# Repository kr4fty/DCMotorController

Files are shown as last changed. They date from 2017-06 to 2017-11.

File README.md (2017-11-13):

# DCMotorController

Control de lazo cerrado para motores DC utilizando un ATMEGA328p (corazón del
  Arduino UNO) y un puente H tipo L293.

<!-- TOC depthFrom:1 depthTo:6 withLinks:1 updateOnSave:1 orderedList:0 -->

- [DCMotorController](#dcmotorcontroller)
	- [Descripción](#descripcin)
	- [Funcionamiento](#funcionamiento)
		- [Parámetros PID](#parmetros-pid)
	- [Características:](#caractersticas)
	- [Firmware](#firmware)
		- [Dependencias](#dependencias)
	- [Hardware](#hardware)
		- [Esquematico](#esquematico)
	- [Video](#video)
	- [Motores de corriente continua](#motores-de-corriente-continua)
		- [Ventajas de los Motores DC frente a los PaP](#ventajas-de-los-motores-dc-frente-a-los-pap)
		- [Desventajas de los Motores DC frente a los PaP](#desventajas-de-los-motores-dc-frente-a-los-pap)
	- [Proyectos Similares](#proyectos-similares)
	- [Licencia](#licencia)
	- [Autor](#autor)

<!-- /TOC -->

<p align="center">
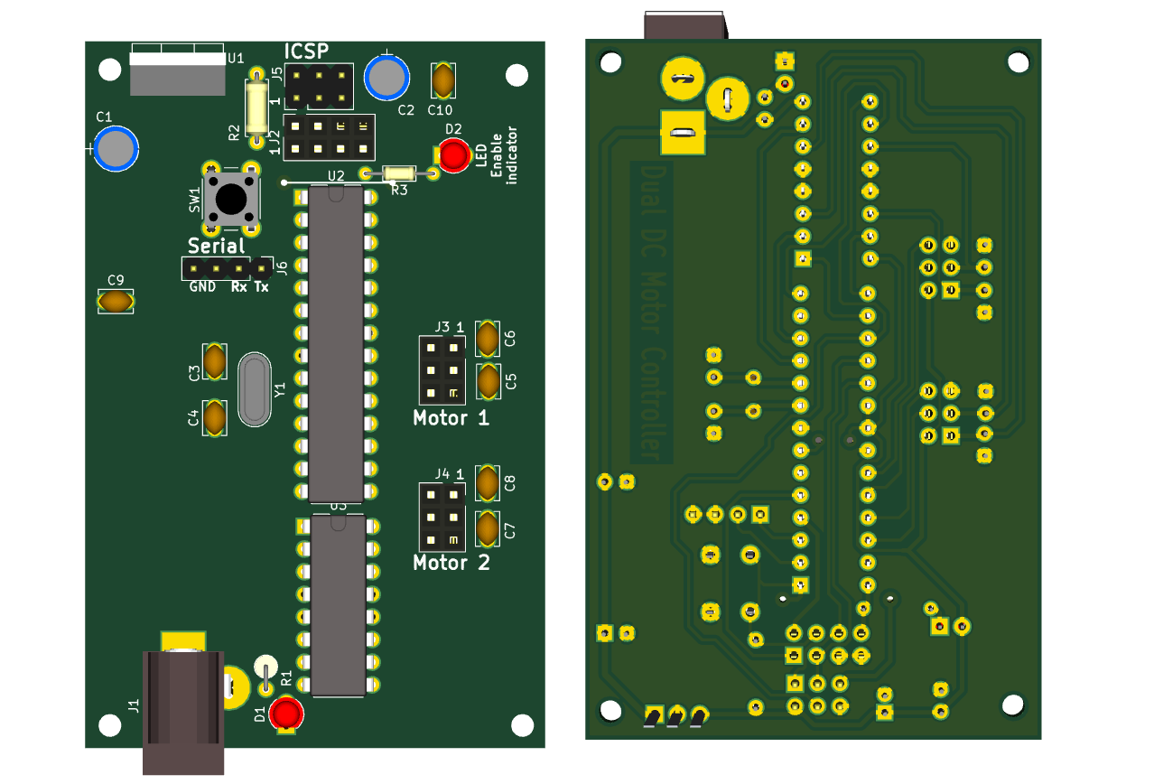
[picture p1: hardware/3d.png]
  
</p>

## Descripción
Este es una pequeña implementación de la librería [ArduinoPID](https://github.com/br3ttb/Arduino-PID-Library), para el control
de motores de corriente continua, DC, que cuenten con un encoder acoplado a su
eje.

Cuenta con soporte para **uno** o **dos** motores, dependiendo de como este
configurado dentro de _**motor.h**_.

La idea principal del proyecto es la de utilizar MOTORES DC/Servos en proyectos
de construcción de CNC en lugar de los tradicionales Motores Paso a Paso (PaP).

El sistema es compatible a nivel de pins de control, con los driver para motores
PaP, **STEP** y **DIR**, como por ejemplo el [Pololu A4988](https://www.pololu.com/product/1182).

## Funcionamiento
Un Arduino cargado con **GRBL**, por ejemplo, envía un pulso a través del pin **STEP**. Cada pulso que recibe el driver le dice al motor que tiene que avanzar un micropaso.

Luego por medio del pin **DIR** obtenemos la dirección de avance, si queremos ir en el sentido de las agujas del reloj, o al contrario.

De esta forma, cada vez que el driver recibe un pulso en el pin **STEP**, el circuito comprueba el estado del pin **DIR**, y alimenta las bobinas del motor en el orden adecuado.

### Parámetros PID
El proceso de sintonizado del PID se hizo de forma experimental, prueba/error, tratando de tener tanto el **overshoot** como el **tiempo de establecimiento** los mas chicos posibles.
Se llego a la conclusión que para el par de motores utilizados, los parámetros que mejor se ajustaban fueron los siguientes:

  * Setpoint > 50: </br>
      Kp = 10 // Agresive Kp</br>
      Ki = 1 // Agresive Ki</br>
      Kd = 0.01 // Agresive Kd</br>

  * Setpoint =< 50:</br>
      Kp = 5  // Conservative Kp</br>
      Ki = 0.1  // Conservative Ki</br>
      Kd = 0.001  // Conservative Kd</br>

Dependiendo del tipo de Motor/Servo utilizados, estos parámetros deberán ser cambiados. Esto ultimo se realizara modificando los prarametros AGGKp,AGGKi, AGGKd, CONSKp, CONSKi y CONSKd, dentro de **motor.h**

## Características:
  * El conjunto Driver-Servo/Motor remplaza al conjunto Driver-Motor/PaP
  * El corazón del sistema es un chip **ATMEGA328p**
  * Se puede controlar uno o dos motores simultáneamente
  * El Driver tiene cuatro señales de control: **DIR**, **STEP**, **ENABLE** y **RESET**
  * Cada motor puede ser controlado de forma independiente por medio de **DIR** y
    **STEP**
  * El sistema de control esta basado en un sistema PID
  * El PWM trabaja a una frecuencia de 31.25KHz, imperceptible al oído humano
  * Cuenta con un salida por puerto serie para depuración
  * Tanto las señales de entrada de los STEPs como las de los encoders, utilizan
    interrupciones del tipo **PIN CHANGE** (PCI)
  * El diseño del **PCB** fue realizado en [KiCAD](https://github.com/KiCad/)
  * La etapa de potencia de los motores fue realizada con un **puente H** del tipo L293D

## Firmware
### Dependencias
El proyecto depende de cuatro librerías:
  * [ArduinoPID](https://github.com/br3ttb/Arduino-PID-Library): Librería principal con la que se realiza el control de lazo
    cerrado
  * [EnableInterrupt](https://github.com/GreyGnome/EnableInterrupt): Encargada de vincular las interrupciones del tipo Pin-change con la respectiva ISR.
  * [EncoderPCI](https://github.com/kr4fty/EncoderPCI): Librería encargada de manejar los Encoders
  * [DCMotorServoPCI](https://github.com/kr4fty/DCMotorServoPCI): Es la librería en si, que realiza la gestión y el control del
    motor dc

## Hardware
Pins utilizados:

<table>
	<tr><th></th><th> Motor 1 </th></tr>
	<tr><th> <b>Arduino Pin</b> </th><th> <b>Descripción</b> </th></tr>
	<tr><td>10 </td><td> pwmX, chip enable 1 del L293D </td></tr>
	<tr><td>6  </td><td> in1X, salida hacia el pin 2, IN1, del L293D </td></tr>
	<tr><td>5  </td><td> in2X, salida hacia el pin 7, IN2, del L293D </td></tr>
	<tr><td>A2 </td><td> inAX, entrada A desde el encoder </td></tr>
	<tr><td>A3 </td><td> inBX, entrada B desde el encoder </td></tr>
	<tr><td>2  </td><td> stepX, entrada STEP proveniente del otro Arduino cargado con GRBL </td></tr>
	<tr><td>12 </td><td> dirX, entrada DIR proveniente del otro Arduino cargado con GRBL </td></tr>
</table>

<table>
	<tr><th></th><th> Motor 2 </th></tr>
	<tr><th> <b>Arduino Pin</b> </th><th> <b>Descripción</b> </th></tr>
	<tr><td> 11 </td><td> pwmY, chip enable 2 del L293D </td></tr>
	<tr><td> 8 </td><td> in1Y, salida hacia el pin 10, IN3, del L293D </td></tr>
	<tr><td> 9 </td><td> in2Y, salida hacia el pin 15, IN4, del L293D </td></tr>
	<tr><td> A0 </td><td> inAY, entrada A desde el encoder </td></tr>
	<tr><td> A1 </td><td> inBY, entrada B desde el encoder </td></tr>
	<tr><td> 3 </td><td> stepY, entrada STEP </td></tr>
	<tr><td> 13 </td><td> dirY, entrada DIR </td></tr>
</table>

<table>
	<tr><th></th><th> Global </th></tr>
	<tr><th> <b>Arduino Pin</b> </th><th> <b>Descripción</b> </th></tr>
	<tr><td> A5 </td><td> entrada ENABLE </td></tr>
	<tr><td> Rst </td><td> Reset del driver </td></tr>
</table>

### Esquematico

<p align="center">
  <br><br>
  <b>Circuito</b><br>
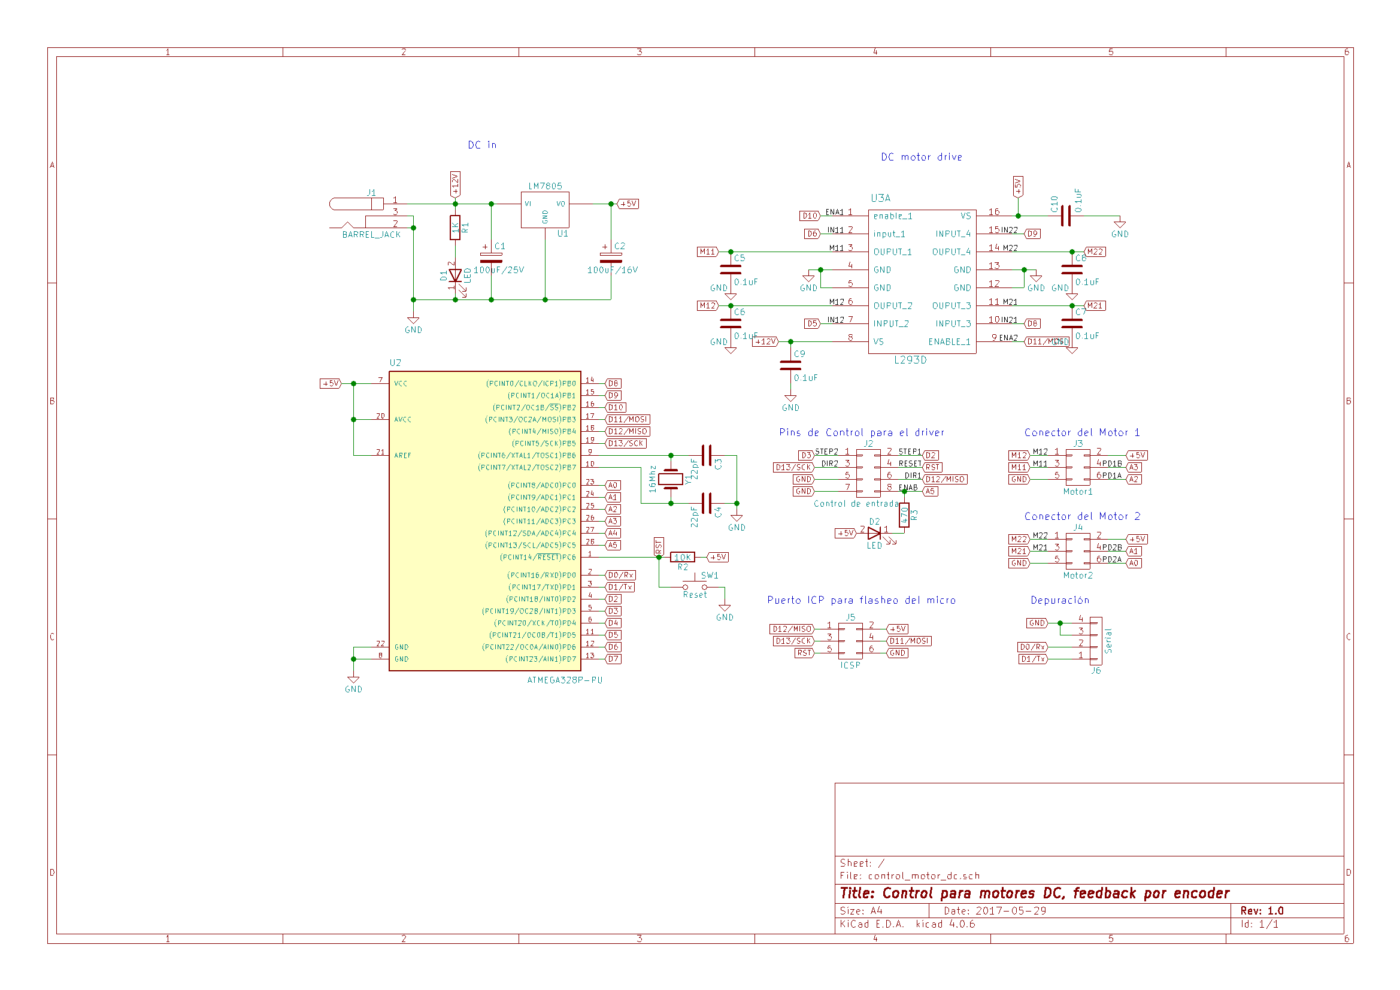
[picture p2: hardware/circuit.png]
  
  <br>
</p>

## Video
<p align="center">
  <b>YouTube</b><br>
  <a href="https://www.youtube.com/watch?v=HcTcVE0kusM">
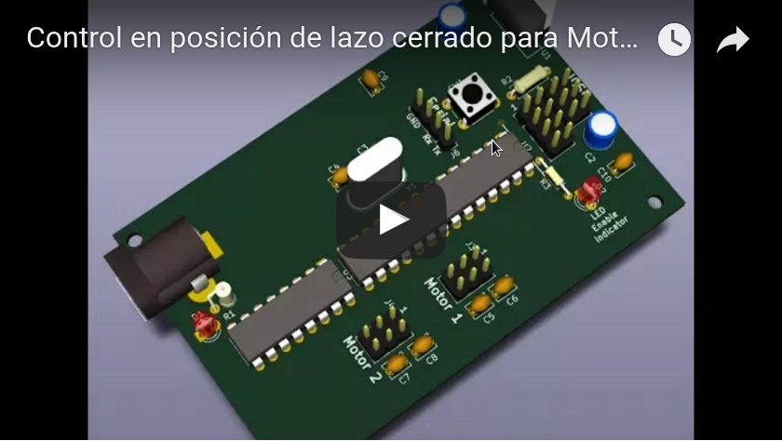
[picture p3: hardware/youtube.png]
  
  </a>
</p>

## Motores de corriente continua

### Ventajas de los Motores DC frente a los PaP
  * Poseen gran velocidad de giro
  * Alta aceleración/Par inicial
  * Son silenciosos
  * Movimiento suave y sin saltos
  * Control medianamente sencilla
  * Electrónica mas sencilla
  * Utiliza realimentación para el control del sistema
  * Debido a este ultimo, tiene alta precisión en posición (depende fuertemente
    del encoder acoplado)

### Desventajas de los Motores DC frente a los PaP
  * La potencia de funcionamiento pico sólo se desarrolla a altas velocidades
  * Debido a sus altas velocidades estos pueden calentarse mas rápidamente
    (podría necesitar un sistemas de ventilación)
  * Inercia mas elevada (depende de la  velocidad y la carga acoplada al eje)

## Proyectos Similares
  * [ServoStrap](https://github.com/danithebest91/ServoStrap) por _danithebest91_
  * [SuryaProCell-CNC](https://github.com/suryaprocell/SuryaProCell-CNC) por _suryaprocell_
  * [DC-Servo-Controller](https://github.com/makerbot/DC-Servo-Controller) por _makerbot_
  * [dcservo](https://github.com/misan/dcservo) por _misan_

## Licencia

GPLv2

## Autor

Tapia Favio

## Feedback

Por favor agradecería que me envies cualquier duda y/o comentario para mejorar el proyecto, gracias.

Mail: technicc (at) gmail.com

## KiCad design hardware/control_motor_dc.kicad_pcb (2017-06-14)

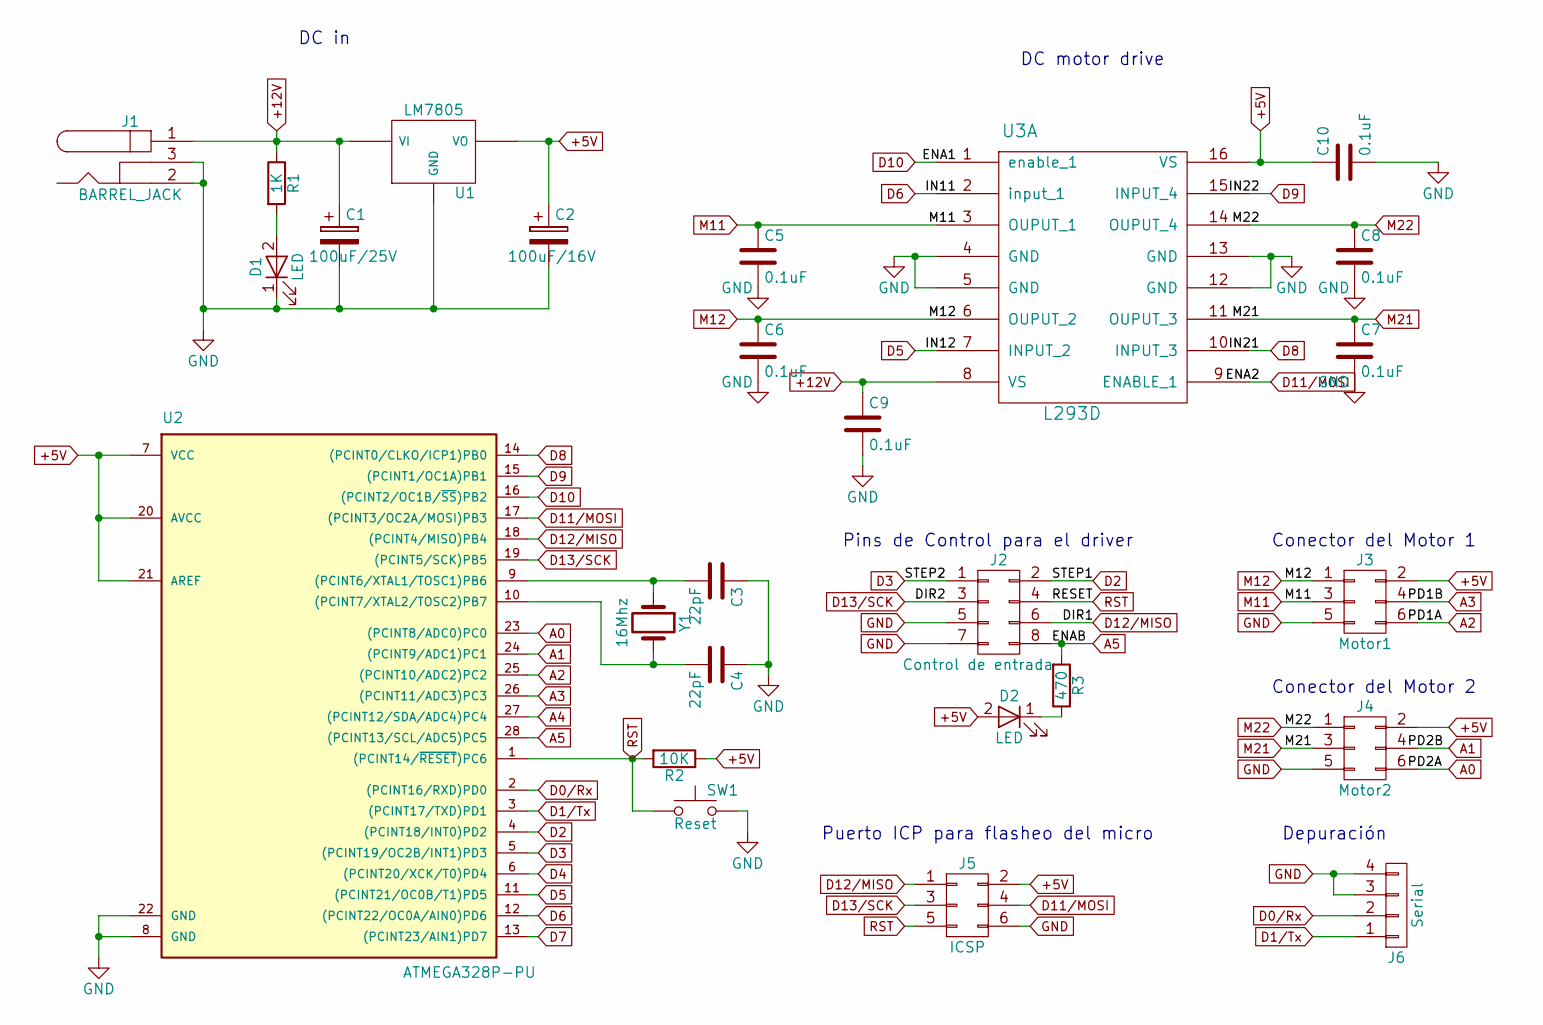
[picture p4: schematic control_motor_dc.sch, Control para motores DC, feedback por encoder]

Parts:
C1: 100uF/25V; CP_Radial_D5.0mm_P2.50mm
C2: 100uF/16V; CP_Radial_D5.0mm_P2.00mm
C3, C4: 22pF; C_Disc_D3.8mm_W2.6mm_P2.50mm
C5, C6, C7, C8, C9, C10: 0.1uF; C_Disc_D3.8mm_W2.6mm_P2.50mm
D1, D2: LED; LED_D3.0mm
J1: BARREL_JACK; JACK_ALIM
J2: Control de entrada; Socket_Strip_Straight_2x04_Pitch2.54mm
J3: Motor1; Socket_Strip_Straight_2x03_Pitch2.54mm
J4: Motor2; Socket_Strip_Straight_2x03_Pitch2.54mm
J5: ICSP; Pin_Header_Straight_2x03_Pitch2.54mm
J6: Serial; Pin_Header_Straight_1x04_Pitch2.54mm
R1: 1K; R_Axial_DIN0207_L6.3mm_D2.5mm_P2.54mm_Vertical
R2: 10K; R_Axial_DIN0207_L6.3mm_D2.5mm_P7.62mm_Horizontal
R3: 470; R_Axial_DIN0204_L3.6mm_D1.6mm_P7.62mm_Horizontal
SW1: Reset; SW_PUSH_6mm
U1: LM7805; TO-220_Vertical-fav
U2: ATMEGA328P-PU; DIP-28_W7.62mm
U3: L293D; DIP-16_W7.62mm
Y1: 16Mhz; Crystal_HC52-6mm_Vertical

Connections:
+5V: C2.1, C10.1, D2.2 (A), J3.2, J4.2, J5.2, R2.1, U1.VO, U2.7 (VCC), U2.20 (AVCC), U2.21 (AREF), U3.16 (VS)
+12V: C1.1, C9.1, J1.1, R1.1, U1.VI, U3.8 (VS)
A0: J4.6, U2.23 ((PCINT8/ADC0)PC0)
A1: J4.4, U2.24 ((PCINT9/ADC1)PC1)
A2: J3.6, U2.25 ((PCINT10/ADC2)PC2)
A3: J3.4, U2.26 ((PCINT11/ADC3)PC3)
A4: U2.27 ((PCINT12/SDA/ADC4)PC4)
A5: J2.8, R3.2, U2.28 ((PCINT13/SCL/ADC5)PC5)
D0/Rx: J6.2, U2.2 ((PCINT16/RXD)PD0)
D1/Tx: J6.1, U2.3 ((PCINT17/TXD)PD1)
D2: J2.2, U2.4 ((PCINT18/INT0)PD2)
D3: J2.1, U2.5 ((PCINT19/OC2B/INT1)PD3)
D4: U2.6 ((PCINT20/XCK/T0)PD4)
D5: U2.11 ((PCINT21/OC0B/T1)PD5), U3.7 (INPUT_2)
D6: U2.12 ((PCINT22/OC0A/AIN0)PD6), U3.2 (input_1)
D7: U2.13 ((PCINT23/AIN1)PD7)
D8: U2.14 ((PCINT0/CLKO/ICP1)PB0), U3.10 (INPUT_3)
D9: U2.15 ((PCINT1/OC1A)PB1), U3.15 (INPUT_4)
D10: U2.16 ((PCINT2/OC1B/~SS~)PB2), U3.1 (enable_1)
D11/MOSI: J5.4, U2.17 ((PCINT3/OC2A/MOSI)PB3), U3.9 (ENABLE_1)
D12/MISO: J2.6, J5.1, U2.18 ((PCINT4/MISO)PB4)
D13/SCK: J2.3, J5.3, U2.19 ((PCINT5/SCK)PB5)
GND: C1.2, C2.2, C3.1, C4.1, C5.2, C6.2, C7.2, C8.2, C9.2, C10.2, D1.1 (K), J1.2, J1.3, J2.5, J2.7, J3.5, J4.5, J5.6, J6.3, J6.4, SW1.2, U1.GND, U2.8 (GND), U2.22 (GND), U3.4 (GND), U3.5 (GND), U3.12 (GND), U3.13 (GND)
M11: C5.1, J3.3, U3.3 (OUPUT_1)
M12: C6.1, J3.1, U3.6 (OUPUT_2)
M21: C7.1, J4.3, U3.11 (OUPUT_3)
M22: C8.1, J4.1, U3.14 (OUPUT_4)
unnamed: C3.2, U2.9 ((PCINT6/XTAL1/TOSC1)PB6), Y1.1
unnamed: C4.2, U2.10 ((PCINT7/XTAL2/TOSC2)PB7), Y1.2
unnamed: D1.2 (A), R1.2
unnamed: D2.1 (K), R3.1
RST: J2.4, J5.5, R2.2, SW1.1, U2.1 ((PCINT14/~RESET~)PC6)

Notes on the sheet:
DC motor drive
Pins de Control para el driver
Puerto ICP para flasheo del micro
Conector del Motor 1
Conector del Motor 2
Depuración
DC in

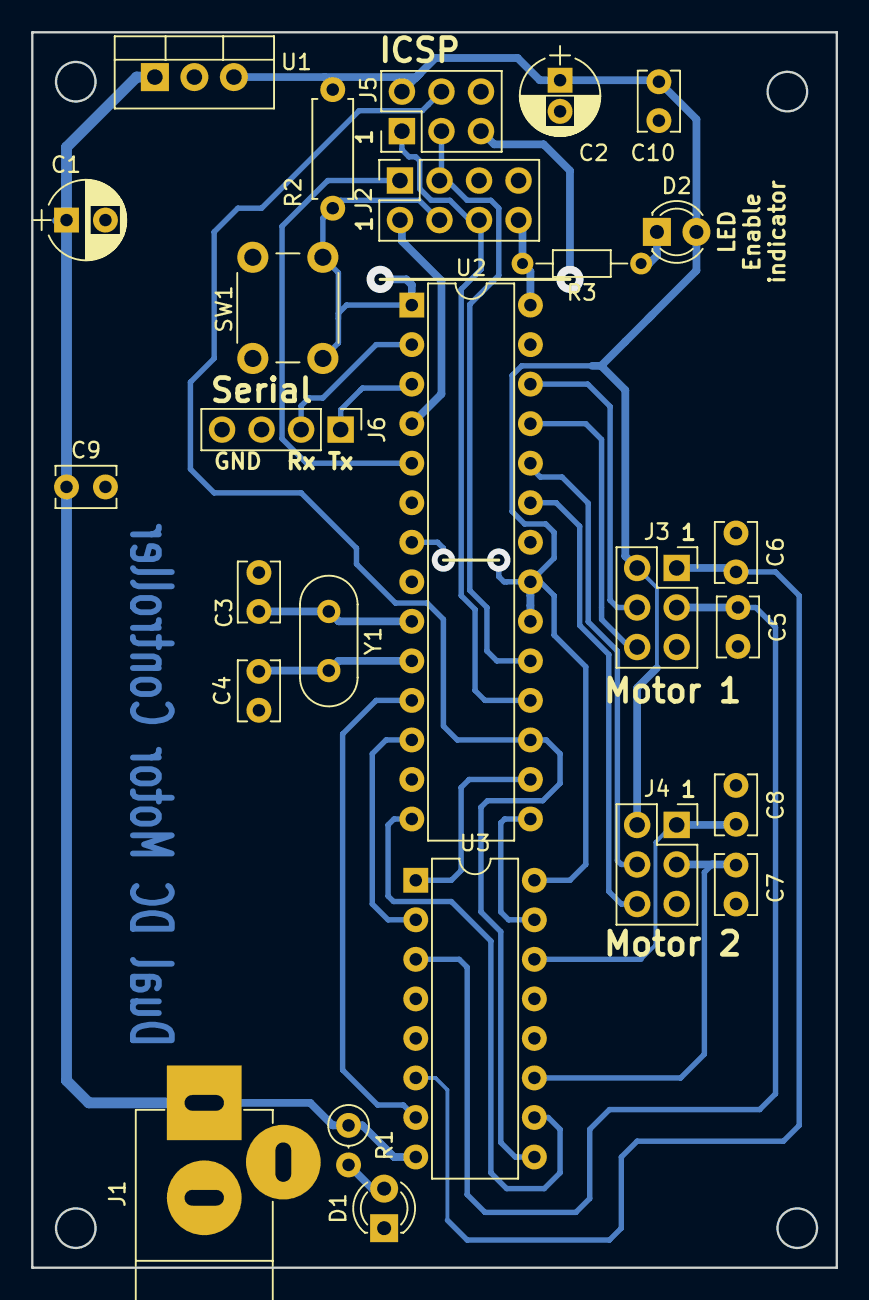
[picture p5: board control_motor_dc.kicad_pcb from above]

Board: 2 copper layers, 51.7 x 79.4 mm, 26 parts (0 on the bottom side), 29 nets.

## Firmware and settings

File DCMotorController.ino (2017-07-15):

#define LIBCALL_ENABLEINTERRUPT   // Para evitar conflictos de compilacion
                                  // por parte de la libreria EnableInterrupt
#include <Arduino.h>
#include <DCMotorServo.h>
#include <EnableInterrupt.h>
#include "motor.h"

#ifndef PIN_TO_BASEREG
  #define PIN_TO_BASEREG(pin) (portInputRegister(digitalPinToPort(pin)))
#endif
#ifndef PIN_TO_BITMASK
  #define PIN_TO_BITMASK(pin) (digitalPinToBitMask(pin))
#endif
#ifndef DIRECT_PIN_READ
  #define DIRECT_PIN_READ(base, mask) (((*(base)) & (mask)) ? 1 : 0)
#endif

typedef struct {
                volatile IO_REG_TYPE * pin_register;
                IO_REG_TYPE            pin_bitmask;
} Pin_internal_state_t;

double  aggKp=  AGGKp;    // Agresive Kp
double  aggKi=  AGGKi;    // Agresive Ki
double  aggKd=  AGGKd;    // Agresive Kd
double  consKp= CONSKp;   // Conservative Kp
double  consKi= CONSKi;   // Conservative Ki
double  consKd= CONSKd;   // Conservative Kd

Pin_internal_state_t pinEnable;
volatile bool enable;   // true: stop, false: run, es ACTIVO en BAJO

#ifdef MOTOR1
  DCMotorServo xAxis = DCMotorServo(in1X, in2X, pwmX, inAX, inBX);
  double actualPositionX;
  volatile double targetX=0;
  Pin_internal_state_t pinDirX;
#endif

#ifdef MOTOR2
  DCMotorServo yAxis = DCMotorServo(in1Y, in2Y, pwmY, inAY, inBY);
  double actualPositionY;
  volatile double targetY=0;
  Pin_internal_state_t pinDirY;
#endif

#ifdef MOTOR1
  static void stepCounterX()
  {
    if(DIRECT_PIN_READ(pinDirX.pin_register, pinDirX.pin_bitmask))
      targetX--;
    else
      targetX++;
  }
#endif

#ifdef MOTOR2
  static void stepCounterY()
  {
    if(DIRECT_PIN_READ(pinDirY.pin_register, pinDirY.pin_bitmask))
      targetY--;
    else
      targetY++;
  }
#endif

static void enableISR()
{
  if(DIRECT_PIN_READ(pinEnable.pin_register, pinEnable.pin_bitmask))
    enable = false; // pinEnable = 1, driver stop
  else
    enable = true;  // pinEnable = 0, driver enabled
}

void setup()
{
  noInterrupts();

  #ifdef MOTOR1
    pinMode(pwmX, OUTPUT);
    pinMode(in1X, OUTPUT);
    pinMode(in2X, OUTPUT);
    pinMode(stepX, INPUT_PULLUP); // Step
    pinMode(dirX, INPUT_PULLUP);  // Direction

    pinDirX.pin_register = PIN_TO_BASEREG(dirX);
    pinDirX.pin_bitmask = PIN_TO_BITMASK(dirX);

    enableInterrupt(stepX, stepCounterX, RISING);   // attach

    xAxis.myPID->SetTunings(aggKp,aggKi,aggKd);
    xAxis.setPWMSkip(40);
    xAxis.setAccuracy(1);
    xAxis.myPID->SetSampleTime(1);

    xAxis.setCurrentPosition(0);
    xAxis.moveTo(targetX);
  #endif

  #ifdef MOTOR2
    pinMode(pwmY, OUTPUT);
    pinMode(in1Y, OUTPUT);
    pinMode(in2Y, OUTPUT);
    pinMode(stepY, INPUT_PULLUP); // Step
    pinMode(dirY, INPUT_PULLUP);  // Direction

    pinDirY.pin_register = PIN_TO_BASEREG(dirY);
    pinDirY.pin_bitmask = PIN_TO_BITMASK(dirY);

    enableInterrupt(stepY, stepCounterY, RISING);   // attach

    yAxis.myPID->SetTunings(aggKp,aggKi,aggKd);
    yAxis.setPWMSkip(40);
    yAxis.setAccuracy(1);
    yAxis.myPID->SetSampleTime(1);

    yAxis.setCurrentPosition(0);
    yAxis.moveTo(targetY);
  #endif


    pinMode(ena, INPUT_PULLUP);  // Enable
    pinEnable.pin_register = PIN_TO_BASEREG(ena);
    pinEnable.pin_bitmask = PIN_TO_BITMASK(ena);
    enableInterrupt(ena, enableISR, CHANGE);    // attach

  #ifdef PWM31KHZ
    TCCR1B = TCCR1B & 0b11111000 | 1; // pwm a 31Kh para el pin 10, TIMER 1
    TCCR2B = TCCR2B & 0b11111000 | 1; // y para el 11, TIMER 2
  #endif

  #ifdef DEBUG
    Serial.begin(9600);
    Serial.println("Debug!");
  #endif

  interrupts();
  delay(500);

}

#ifdef DEBUG
  double oldPosX, oldPosY;
#endif

void loop()
{
  if(enable){ // if ENABLE
    #ifdef DEBUG
      #ifdef MOTOR1
        oldPosX = actualPositionX;
      #endif
      #ifdef MOTOR2
        oldPosY = actualPositionY;
      #endif
    #endif

    #ifdef MOTOR1
      xAxis.moveTo(targetX);
      actualPositionX= xAxis.getActualPosition();
      double gapX = abs(targetX-actualPositionX);

      if(gapX < 50)
        xAxis.myPID->SetTunings(consKp,consKi,consKd);  // set Conservative tunning
      else
        xAxis.myPID->SetTunings(aggKp,aggKi,aggKd);     // set Agresive tunning
    #endif

    #ifdef MOTOR2
      yAxis.moveTo(targetY);
      actualPositionY= yAxis.getActualPosition();
      double gapY = abs(targetY-actualPositionY);

      if(gapY < 50)
        yAxis.myPID->SetTunings(consKp,consKi,consKd);  // set Conservative tunning
      else
        yAxis.myPID->SetTunings(aggKp,aggKi,aggKd);;    // set Agresive tunning
    #endif

    #ifdef MOTOR1
      xAxis.run();
    #endif
    #ifdef MOTOR2
      yAxis.run();
    #endif

    #ifdef DEBUG  // DEBUG
      #ifdef MOTOR1
        #ifdef MOTOR2
          if( (oldPosX!=actualPositionX) || (oldPosY!=actualPositionY) ){
        #else
          if(oldPosX!=actualPositionX){
        #endif
            Serial.print(actualPositionX);
            Serial.print(" : ");
            Serial.print(targetX);
            #ifndef MOTOR2
              Serial.println("");
            #endif
          }
      #endif

      #ifdef MOTOR2
        #ifdef MOTOR1
          if( (oldPosX!=actualPositionX) || (oldPosY!=actualPositionY) ){
            Serial.print(" || ");
        #else
          if((oldPosY!=actualPositionY)){
        #endif
            Serial.print(actualPositionY);
            Serial.print(" : ");
            Serial.println(targetY);
          }
      #endif
    #endif      //end DEBUG
  } // end if ENABLE
  else{ //else ENABLE
    #ifdef MOTOR1
      xAxis.stop();
    #endif
    #ifdef MOTOR2
      yAxis.stop();
    #endif
  } //end else ENABLE
} // end loop

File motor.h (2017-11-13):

/*
 * GBRL Mega 2560:
 *   #define X_STEP_BIT    2 // MEGA2560 Digital Pin 24
 *   #define Y_STEP_BIT    3 // MEGA2560 Digital Pin 25
 *   #define Z_STEP_BIT    4 // MEGA2560 Digital Pin 26
 *
 *   #define X_DIRECTION_BIT   7 // MEGA2560 Digital Pin 30 (PC7)
 *   #define Y_DIRECTION_BIT   6 // MEGA2560 Digital Pin 31 (PC6)
 *   #define Z_DIRECTION_BIT   5 // MEGA2560 Digital Pin 32
 *
 *   #define STEPPERS_DISABLE_BIT   7 // MEGA2560 Digital Pin 13
 *
 * My GRBL config:
 *   $100=75.000    (x, step/mm)
 *   $101=75.000    (y, step/mm)
 *   $102=75.000    (z, step/mm)
 *   $110=2500.000  (x max rate, mm/min)
 *   $111=2500.000  (y max rate, mm/min)
 *   $112=2500.000  (z max rate, mm/min)
 *   $120=75.000    (x accel, mm/sec^2)
 *   $121=75.000    (y accel, mm/sec^2)
 *   $122=75.000    (z accel, mm/sec^2)
 *   $130=200.000   (x max travel, mm)
 *   $131=200.000   (y max travel, mm)
 *   $132=200.000   (z max travel, mm)
 *
 */

#ifndef _MOTOR_H
#define _MOTOR_H

#define MOTOR1      // Estara habilitado si se esta definido
#define MOTOR2      // Pueden estar tanto el uno, el otro o ambos

//#define DEBUG     // Muestrar posicion actual y estado de los setPoins
#define PWM31KHZ    // Habilito la salida de pwm, OC1x y OC2x, a 31.25 KHz
                    // Si no se define, la frecuencia pwm por dafult es de 976Hz

#if (not defined(MOTOR1)) && (not defined(MOTOR2)) && (not defined(MOTOR2))
  #error seleccione AL MENOS un Motor
#endif

  #ifdef MOTOR1
    #define pwmX 10 // Habilito/Desabilito, chip enable, del L293D
    #define in1X  6 // Salida hacia el pin 2, IN1, del L293D
    #define in2X  5 // Salida hacia el pin 7, IN2, del L293D
    #define inAX A2 // Entrada INA desde el encoder
    #define inBX A3 // Entrada INB desde el encoder
    #define stepX 2 // Entrada STEP proveniente del otro Arduino cargado con GRBL
    #define dirX 12 // Entrada DIR proveniente del otro Arduino cargado con GRBL
  #endif

  #ifdef MOTOR2
    #define pwmY 11
    #define in1Y  8
    #define in2Y  9
    #define inAY A0
    #define inBY A1
    #define stepY 3
    #define dirY 13
  #endif

  #define ena A5    // Entrada ENABLE proveniente del Arduino cargado con GRBL
                    // es activo en nivel bajo

  // PID Parameters
  #define AGGKp      10   // Agresive Kp
  #define AGGKi       1   // Agresive Ki
  #define AGGKd    0.01   // Agresive Kd

  #define CONSKp      5   // Conservative Kp
  #define CONSKi    0.1   // Conservative Ki
  #define CONSKd  0.001   // Conservative Kd

#endif
